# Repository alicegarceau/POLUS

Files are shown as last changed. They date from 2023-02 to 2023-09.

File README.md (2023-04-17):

# POLUS

Démonstrations des habiletés de P-O le petit robot :

<a href="http://www.youtube.com/watch?feature=player_embedded&v=78BupOIvDnI
" target="_blank">Dessin pixels</a>

<a href="http://www.youtube.com/watch?feature=player_embedded&v=hgMGZM_LDB8
" target="_blank">Dessin lignes</a>

## Table des matières
* [Requis matériels](#requis-matériels)
* [Assemblage](#assemblage)
* [Requis logiciels](#requis-logiciels)
* [Installation](#installation)
* [Exécuter le programme](#exécuter-le-programme)
* [License](#license)

## Requis matériels
### Impression 3D
Sur une imprimante 3D avec une capacité d'au moins 250 x 250 x 200mm, imprimer tous les fichiers dans le dossier ([STLs](https://github.com/alicegarceau/POLUS/tree/main/V1_STLs))

### Autres composants mécaniques
- [ ] 1 x Paquet de crayons feutres ([Amazon](https://www.amazon.ca/-/fr/dp/B01LXRJKVY?psc=1&))
- [ ] 2 x Vis M6 x 1 à épaulement de 8 x 55mm ([McMaster-Carr](https://www.mcmaster.com/92981A210/))
- [ ] 2 x Écrous M6
- [ ] 4 x Rondelles M6
- [ ] 1 x Coupleur flexible 5mm à 8mm ([Amazon](https://www.amazon.ca/AFUNTA-Flexible-Couplings-Compatible-Machines/dp/B07JL1QYLS/))
- [ ] 1 x Vis ACME Tr8 x 8mm x 300mm et écrou ([Amazon](https://www.amazon.ca/dp/B08JQ4H6M9?_encoding=UTF8&psc=1&))
- [ ] 3 x Roulements à billes linéaires LM8UU ([Amazon](https://www.amazon.ca/uxcell%C2%AE-Bushing-Linear-Motion-Double/dp/B00X9H22SO/))
- [ ] 4 x Roulements à billes à épaulement 608 ([McMaster-Carr](https://www.mcmaster.com/57155K513/))
- [ ] 26 x Inserts filetés M3 pour plastique ([McMaster-Carr](https://www.mcmaster.com/94180A333/))
- [ ] 32 x Vis SHCS M3 x 14mm
- [ ] 12 x Vis SHCS M2.5 x 6mm
- [ ] 1 x Feuille de contre-plaqué 480 x 480mm
- [ ] 6 x Attaches de plastique (Tyrap) 3 x 100mm min

### Composants électriques
- [ ] 1 x Fil micro-USB de 0.3m
- [ ] 1 x Microcontrôleur OpenCR 1.0 
- [ ] 2 x Servomoteurs Dynamixel XM430-W350
- [ ] 1 x Servomoteur Dynamixel XL430-W250
- [ ] 2 x Servomoteur de type "hobby" Hitech HS-422
- [ ] 1 x Moteur pas-à-pas NEMA17 ([Amazon](https://www.amazon.ca/dp/B06ZYQNBFR?))
- [ ] 1 x Contrôleur de moteur pas-à-pas ([EasyDriver](https://www.sparkfun.com/products/12779))
- [ ] 2 x Interrupteur de fin de course miniature

## Assemblage
### Assemblage électrique
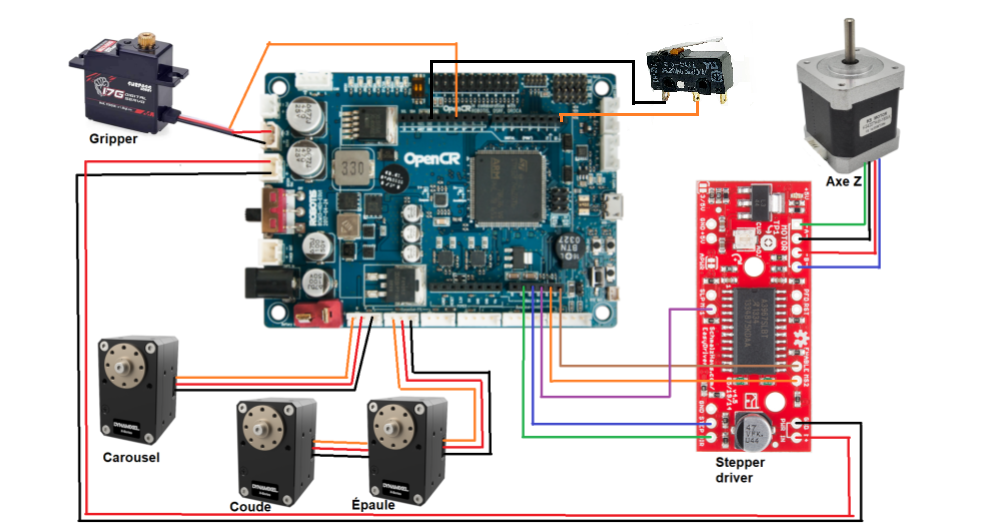
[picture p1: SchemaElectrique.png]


### Assemblage mécanique

Installer les inserts filetés avec un fer à souder à environ 300 deg C dans toutes les pièces qui doivent en recevoir.

#### Avant-bras et pince

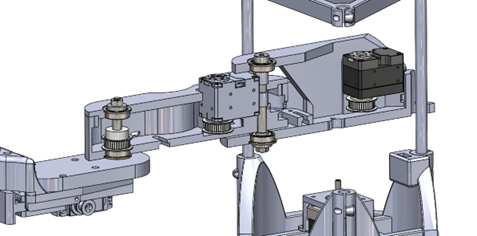
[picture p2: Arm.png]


#### Bras et épaule (plateforme mobile en Z)

#### Base
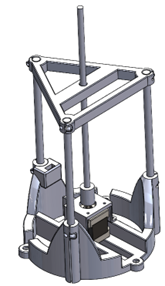
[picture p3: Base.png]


#### Carousel
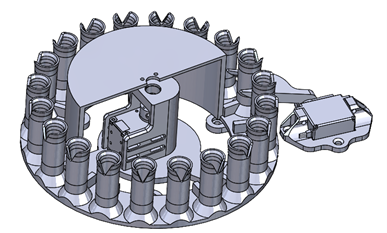
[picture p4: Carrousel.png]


## Requis logiciels
* Arduino IDE version 2 ([arduino](https://www.arduino.cc/en/software))
* Paquet Open-CR du Boards Manager : suivre les instructions d'installation pour Windows ([opencr](https://emanual.robotis.com/docs/en/parts/controller/opencr10/#install-on-windows))

### Fichiers de code du OpenCR
Le dossier Code_OpenCR contient toutes les fonctions en C++ qui s'exécutent sur la carte OpenCR.
- __actuators.cpp__ : Ce fichier contient les fonctions qui contrôlent les actuateurs du projet POLUS, sauf le moteur pas à pas de l'axe Z.
- __stepperZ.cpp__ : Ce fichier contient les fonctions qui contrôlent le moteur pas à pas de l'axe Z. 
- __inverseKinematics.cpp__ : Ce fichier reçoit en entré une valeur cartésienne (X,Y) et retourne deux angles pour les moteurs du bras scara.
- __serialcomm_functions.cpp__: Permet de lire des données depuis un port série, les diviser en parties distinctes et appeler la fonction correspondante en fonction du type de message envoyé.
- __Code_OpenCR.ino__ : Ce fichier est le fichier "main" s'exécutant sur la carte OpenCR.

### Diagramme d'état du code

L'image suivante démontre la relation entre le code s'exécutant sur l'ordinateur (interface utilisateur) et la carte OpenCR.

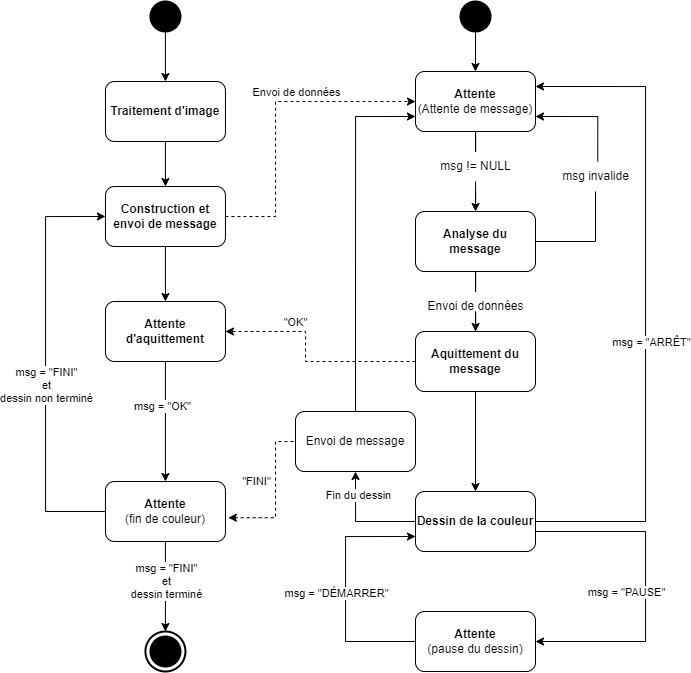
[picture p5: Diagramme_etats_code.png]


## Installation

Sur un PC Windows :
* Ouvrir le fichier Code_OpenCR.ino dans Arduino IDE et brancher la carte OpenCR à l'ordinateur. Dans Arduino IDE, sélectionner le "board" OpenCR et téléverser le code.
* Brancher la carte OpenCR à votre ordinateur avec un fil micro-USB
* Installer les librairies Python suivantes avec pip:
   - pyserial
   - threading
   - PIL
   - os
   - csv
   - numpy
   - colormath
   - tkinter

## Exécuter le programme
- Lancer le programme main.py
- L'interface utilisateur suivant s'ouvre :


- Dans l'interface utilisateur, entrer les bonnes informations dans les différents champs :
   *** Précisions :
   - Le fichier des RGB doit être un fichier .CSV où chaque rangée contient les valeur R,G,B d'un crayon du carrousel. La 1ère ligne du fichier correspond au crayon à      l'index 1 et ainsi de suite. C'est de cette manière que le robot sait quel crayon se trouve à quel endroit dans le carrousel.
   - Le nombre de pixels voulus représente le nombre de pixels pour une dimension. Dans cet exemple, l'image dessinée fera 50x50 pixels.
- Appuyer sur les boutons "Envoyer les noms de fichiers" et "Envoyer la résolution de l'image".
- Fermer l'interface graphique pour lancer le traitement d'image.
- Dans le terminal, un message s'affiche pour choisir le port USB pour établir la liaison série avec le OpenCR (ce message peut prendre plusieurs secondes à             s'afficher).
- L'utilisateur n'a plus rien à faire à partir d'ici.

## License
Apache Version 2.0

Voir [LICENSE](LICENSE)

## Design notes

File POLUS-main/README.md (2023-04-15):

# POLUS
Voir le document "Doc traitement image" pour la documentation des fonctions utilisées pour le traitement d'image (pixeliser_image.py).

- __RGB_20.csv__ : document contenant les 20 RGB des crayons disponibles
- __UI.py__ : création de l'interface utilisateur à l'aide de Tkinter
- __input_UI.py__ : fichier obsolète non utilisé
- __pixeliser_image.html__ : html de la documentation du traitement d'image avec pydoc
- __pixeliser_image.py__ : fonctions utilisées pour le traitement d'image
- __communication.py__ : Fonctions pour initialiser une liaison série, trouver un port disponible, construire et envoyer des messages à l'OpenCR, et lire l'acquittement de ces messages.
- __main.py__ : fonction main
- __image_in.jpg__ : image d'origine
- __image_pix.png__ : image pixélisée
- __image_result.png__ : image du résultat attendu
- __UI2.py__ : 2e version du UI, présentement non fonctionnelle. Cette version est plus épurée.

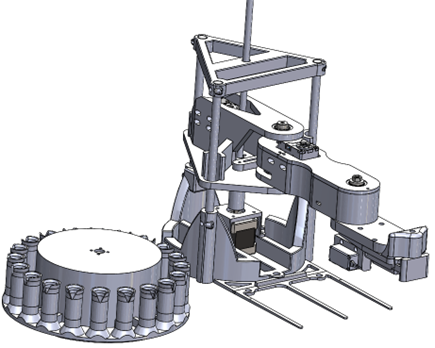
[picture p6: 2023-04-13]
Projet.png

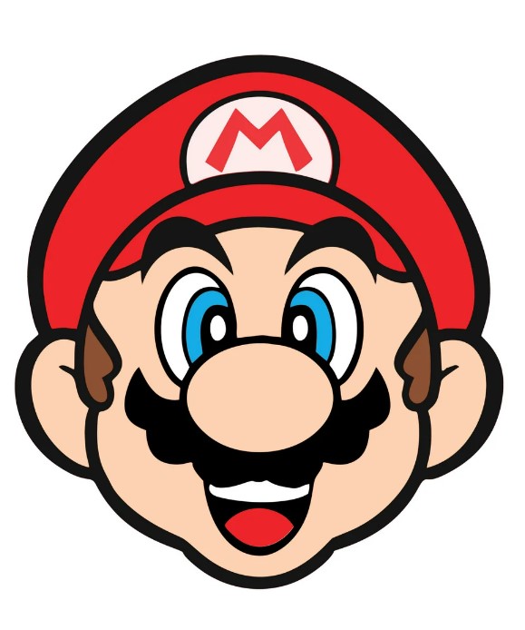
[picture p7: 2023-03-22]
POLUS-main/image_in.jpg

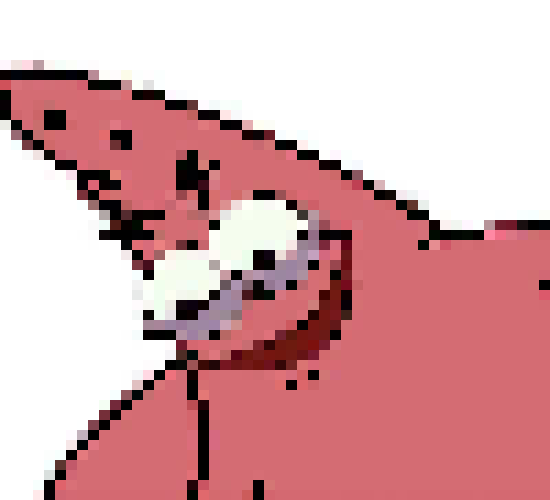
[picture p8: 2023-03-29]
POLUS-main/image_pix.png

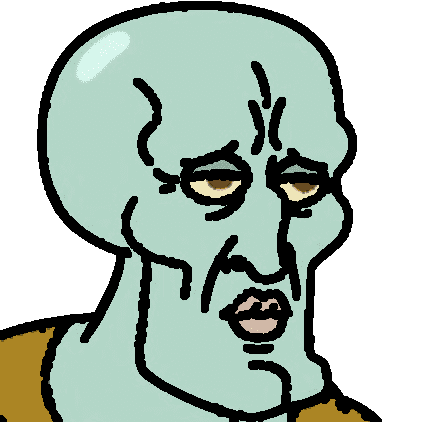
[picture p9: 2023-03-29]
POLUS-main/Carlo1.png

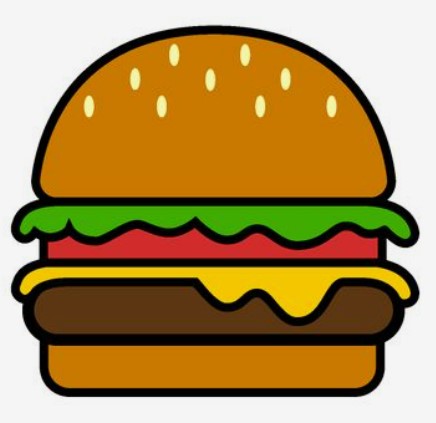
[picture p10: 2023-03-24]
POLUS-main/burger.jpg

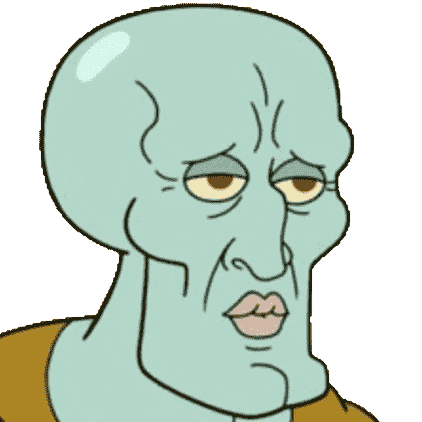
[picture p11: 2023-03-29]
POLUS-main/Carlo.png

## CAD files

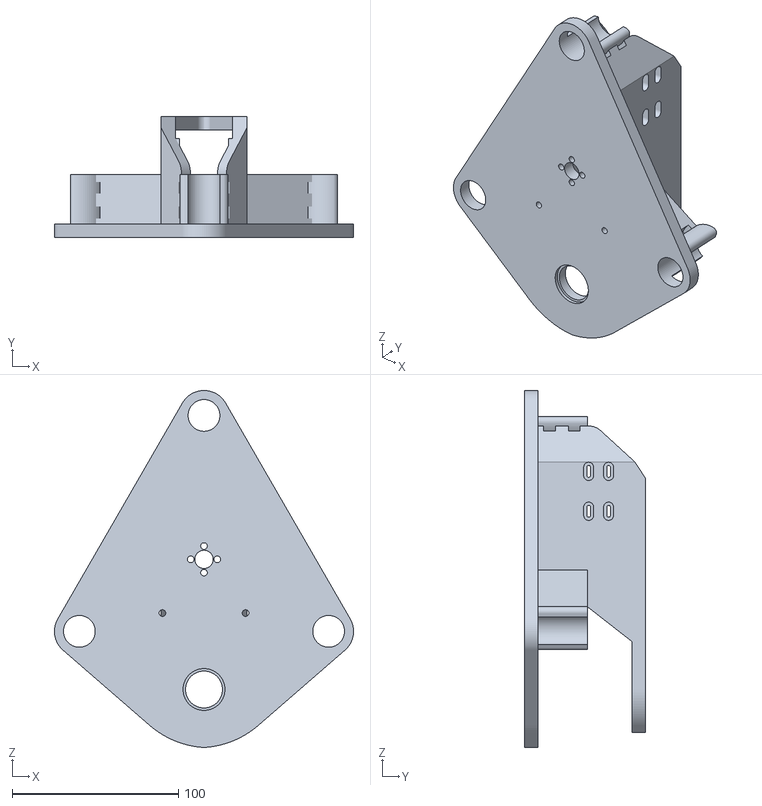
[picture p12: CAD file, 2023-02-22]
V1_STLs/V1_STLs/Arm/PlaqueBottom.STL
180.0 x 72.8 x 214.8

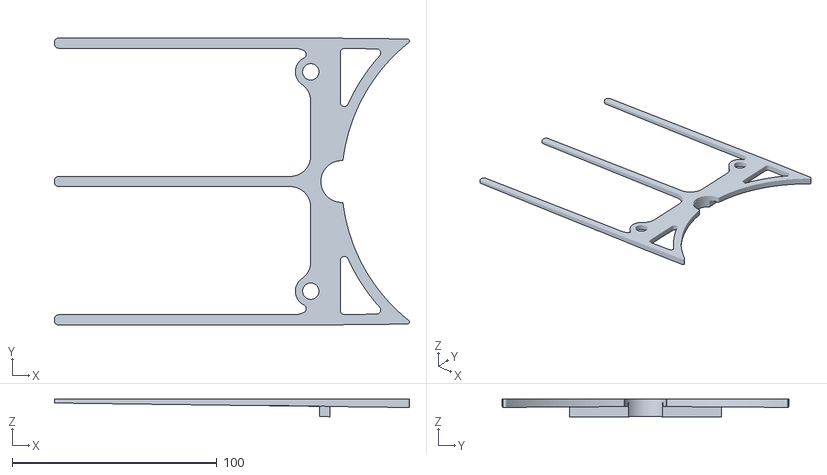
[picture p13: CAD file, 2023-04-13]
V1_STLs/V1_STLs/Base/SpacerV1.STL
173.2 x 140.0 x 8.56

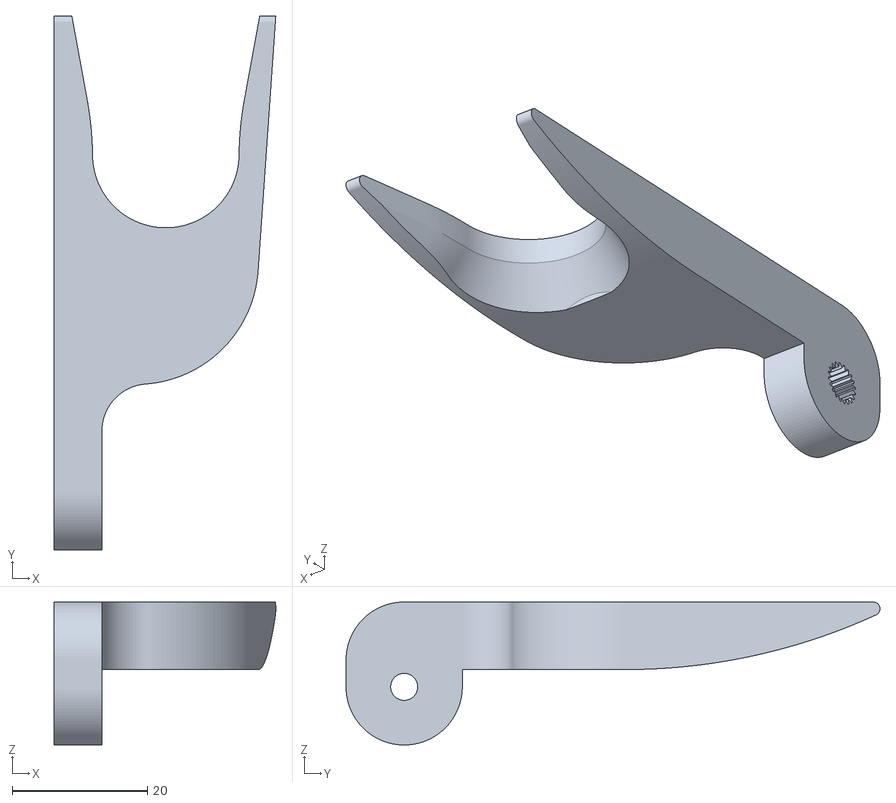
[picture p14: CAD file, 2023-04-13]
V1_STLs/V1_STLs/Carrousel/Centering.STL
32.8 x 79.0 x 21.2

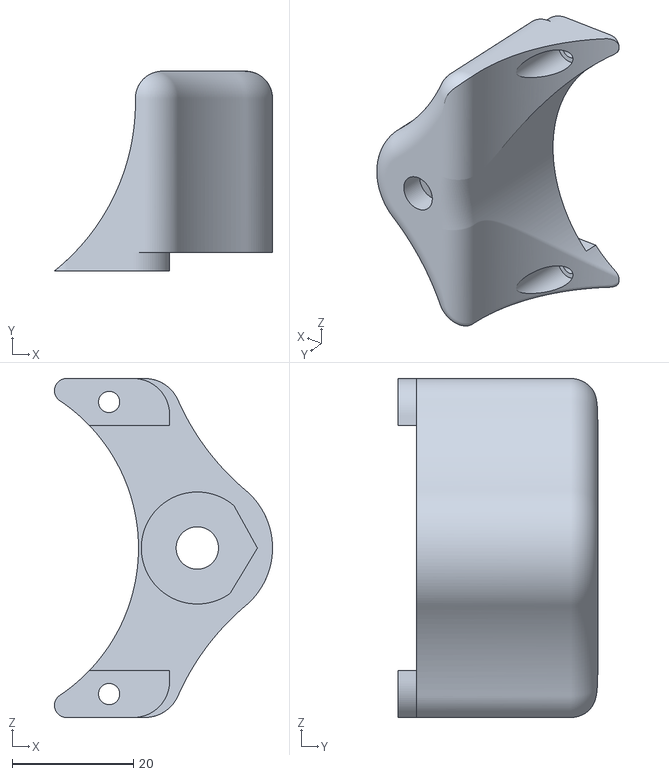
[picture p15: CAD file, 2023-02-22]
V1_STLs/V1_STLs/Pince/SpringCap.STL
36.0 x 33.0 x 56.0

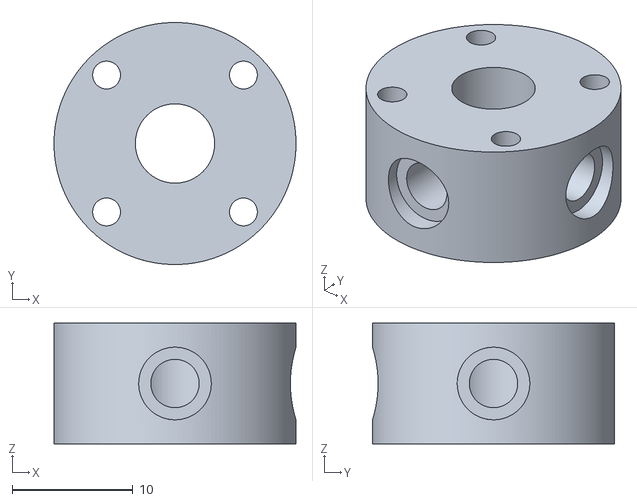
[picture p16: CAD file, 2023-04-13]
V1_STLs/V1_STLs/Pulleys/MotorShaftCoupling.STL
20.0 x 20.0 x 10.0

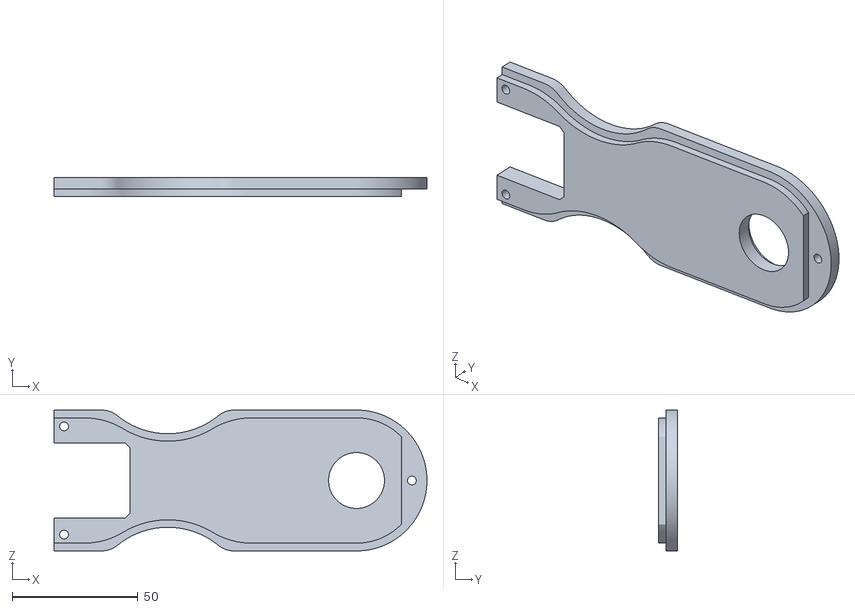
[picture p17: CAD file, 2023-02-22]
V1_STLs/V1_STLs/Arm/Arm1_Cover.STL
148.2 x 7.50 x 56.0

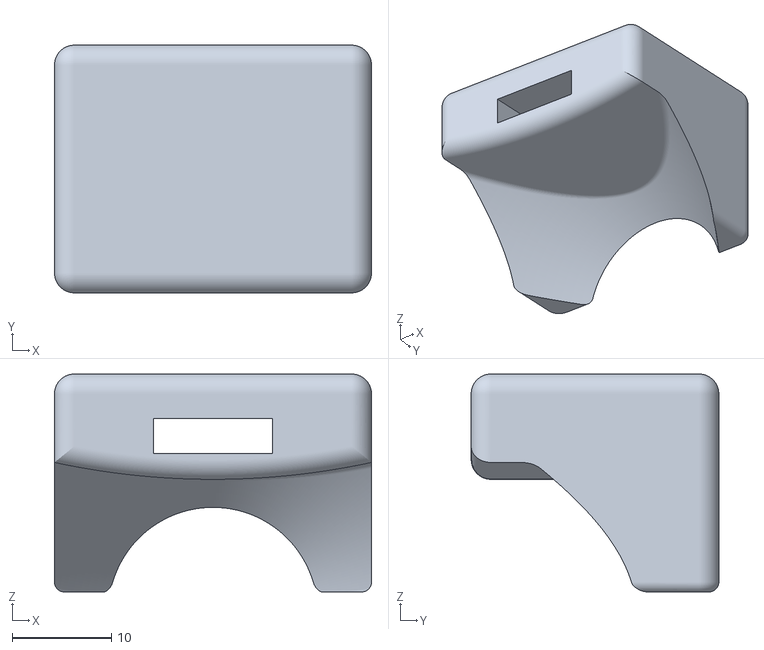
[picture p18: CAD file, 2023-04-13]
V1_STLs/V1_STLs/Base/LimitSwitchMount_V2.STL
32.0 x 25.0 x 22.0

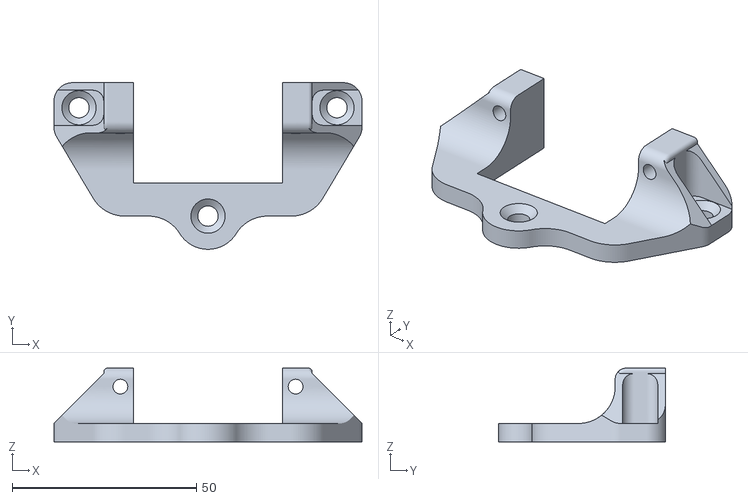
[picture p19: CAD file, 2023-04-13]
V1_STLs/V1_STLs/Carrousel/CenteringServoMount.STL
83.5 x 45.2 x 20.0

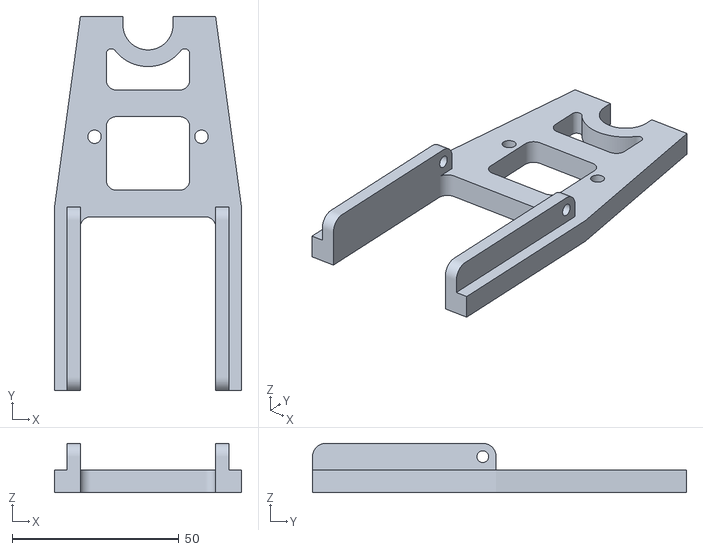
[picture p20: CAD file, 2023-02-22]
V1_STLs/V1_STLs/Pince/ArmMount.STL
56.0 x 112.0 x 14.8

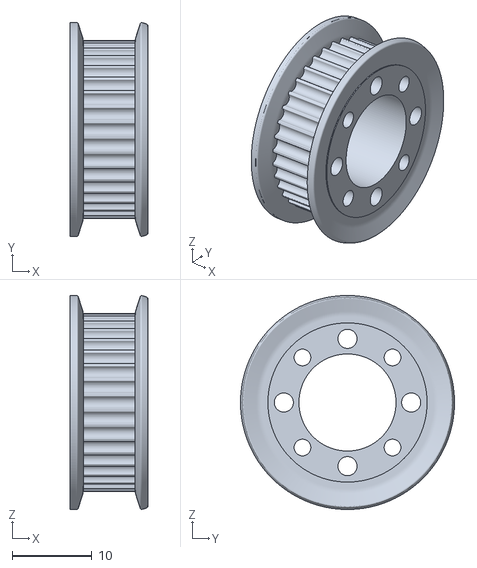
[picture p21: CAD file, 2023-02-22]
V1_STLs/V1_STLs/Pulleys/GT2 36T B5 W10 pulley.stp.STL
9.75 x 26.9 x 26.9

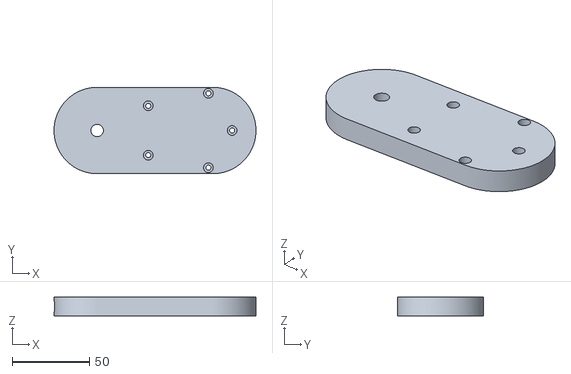
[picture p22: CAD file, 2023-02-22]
V1_STLs/V1_STLs/Arm/Arm2_Shell.STL
131.0 x 56.0 x 12.0

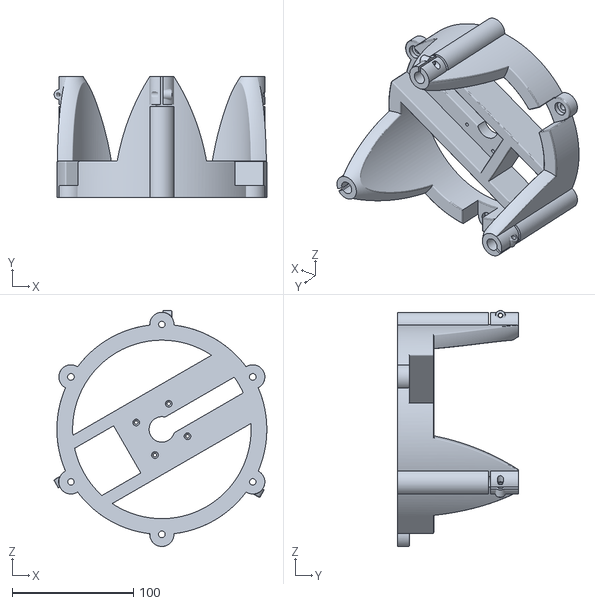
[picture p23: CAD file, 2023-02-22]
V1_STLs/V1_STLs/Base/Base_v4.STL
175.4 x 100.0 x 194.7

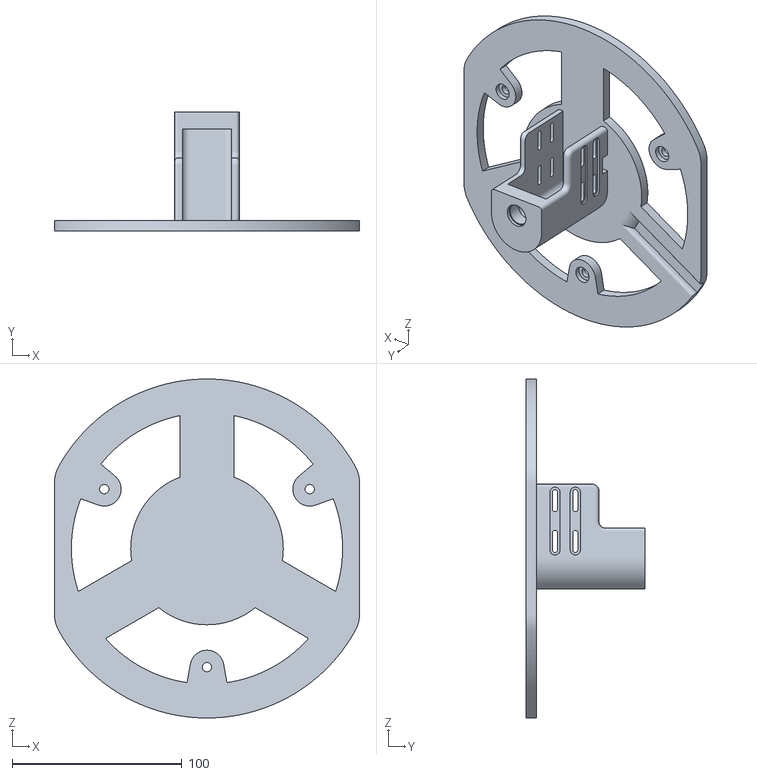
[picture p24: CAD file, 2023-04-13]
V1_STLs/V1_STLs/Carrousel/Carrousel_Base_V3.STL
180.0 x 70.0 x 200.0

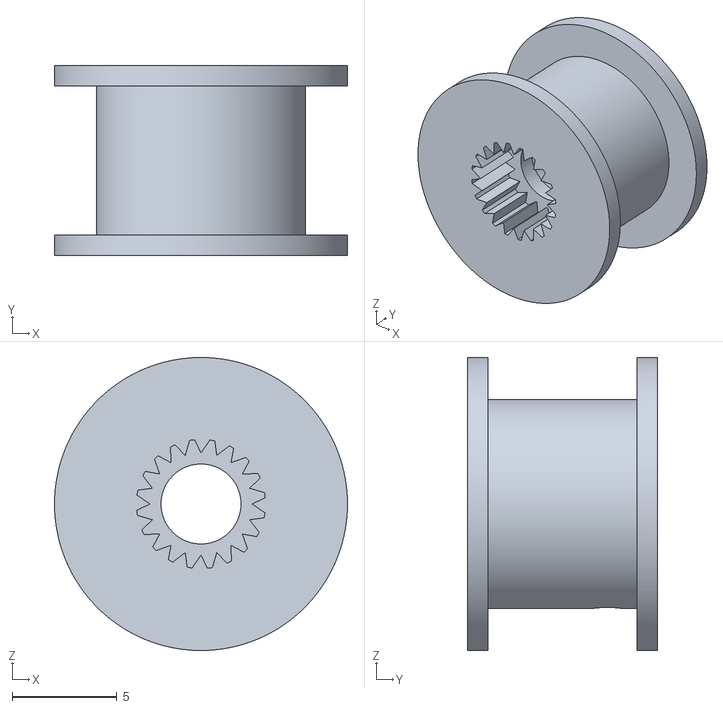
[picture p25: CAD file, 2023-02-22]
V1_STLs/V1_STLs/Pince/Reel.STL
14.0 x 9.10 x 14.0

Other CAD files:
V1_STLs/V1_STLs/Arm/Arm1_Cover2.STL
V1_STLs/V1_STLs/Base/MotorPlate.STL
V1_STLs/V1_STLs/Carrousel/Cloche.STL
V1_STLs/V1_STLs/Pince/JawTest2_2.STL
V1_STLs/V1_STLs/Arm/Arm1_Shell.STL
V1_STLs/V1_STLs/Arm/Tensionner.STL
V1_STLs/V1_STLs/Base/Triangle_Top.STL
V1_STLs/V1_STLs/Pince/Base_V2.STL
V1_STLs/V1_STLs/Pince/JawTest2.STL
V1_STLs/V1_STLs/Pince/Plunger.STL
V1_STLs/V1_STLs/Pince/Spacer.STL
V1_STLs/V1_STLs/Pulleys/GT2 36T Screw.STL
V1_STLs/V1_STLs/Pulleys/GT2-6x60x20.step.STL

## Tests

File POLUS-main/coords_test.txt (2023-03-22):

[2, 50, 50, 921, 922, 923, 924, 925, 971, 972, 973, 974, 975, 976, 977, 1015, 1016, 1017, 1018, 1019, 1022, 1023, 1024, 1025, 1026, 1027, 1029, 1030, 1031, 1032, 1033, 1064, 1065, 1066, 1070, 1071, 1072, 1073, 1074, 1075, 1076, 1077, 1078, 1082, 1083, 1084, 1110, 1111, 1112, 1113, 1114, 1121, 1122, 1123, 1124, 1125, 1126, 1133, 1134, 1135, 1136, 1160, 1161, 1162, 1163, 1164, 1172, 1173, 1174, 1175, 1176, 1184, 1185, 1186, 1187, 1188, 1189, 1209, 1210, 1211, 1212, 1213, 1223, 1224, 1225, 1226, 1235, 1236, 1237, 1238, 1239, 1260, 1261, 1262, 1263, 1264, 1273, 1274, 1275, 1285, 1286, 1287, 1288, 1289, 1310, 1311, 1312, 1313, 1335, 1336, 1337, 1338, 1355, 1356, 1361, 1362, 1363, 1364, 1375, 1385, 1386, 1387, 1392, 1393, 1394, 1404, 1405, 1406, 1412, 1413, 1414, 1420, 1421, 1422, 1423, 1424, 1425, 1426, 1427, 1428, 1435, 1436, 1437, 1442, 1443, 1444, 1445, 1453, 1454, 1455, 1461, 1464, 1465, 1469, 1470, 1471, 1472, 1473, 1474, 1475, 1476, 1477, 1478, 1479, 1480, 1484, 1487, 1493, 1494, 1495, 1503, 1504, 1505, 1506, 1511, 1515, 1518, 1519, 1520, 1521, 1522, 1523, 1524, 1525, 1526, 1527, 1528, 1529, 1530, 1533, 1534, 1537, 1542, 1543, 1544, 1545, 1553, 1554, 1555, 1556, 1561, 1568, 1569, 1570, 1571, 1572, 1573, 1574, 1575, 1576, 1577, 1578, 1579, 1580, 1587, 1592, 1593, 1594, 1595, 1603, 1604, 1605, 1606, 1607, 1610, 1611, 1618, 1619, 1620, 1621, 1622, 1623, 1624, 1625, 1626, 1627, 1628, 1629, 1630, 1638, 1641, 1642, 1643, 1644, 1645, 1654, 1655, 1656, 1657, 1659, 1660, 1661, 1669, 1670, 1671, 1672, 1673, 1674, 1675, 1676, 1677, 1678, 1679, 1687, 1688, 1689, 1691, 1692, 1693, 1694, 1705, 1706, 1707, 1709, 1710, 1711, 1712, 1713, 1720, 1721, 1722, 1723, 1724, 1725, 1726, 1727, 1728, 1736, 1737, 1738, 1741, 1742, 1743, 1744, 1755, 1756, 1757, 1760, 1761, 1762, 1763, 1774, 1785, 1786, 1787, 1788, 1789, 1792, 1793, 1807, 1810, 1811, 1812, 1813, 1814, 1835, 1836, 1837, 1838, 1841, 1860, 1861, 1862, 1863, 1864, 1865, 1866, 1867, 1881, 1882, 1883, 1884, 1885, 1886, 1887, 1888, 1911, 1912, 1913, 1914, 1915, 1916, 1917, 1918, 1930, 1931, 1932, 1933, 1934, 1935, 1936, 1937, 1938, 1962, 1963, 1964, 1965, 1966, 1967, 1968, 1980, 1981, 1982, 1983, 1984, 1985, 1986, 1987, 2013, 2014, 2015, 2016, 2017, 2018, 2030, 2031, 2032, 2033, 2034, 2035, 2065, 2066, 2067, 2068, 2069, 2079, 2080, 2081, 2082, 2083, 2084, 2117, 2118, 2119, 2120, 2129, 2130, 2131, 2169, 2170, 2171, 2178, 2179, 2220, 2221, 2222, 2223, 2225, 2226, 2227, 2228, 2273, 2275, 2276]
[3, 50, 50, 926, 927, 1067, 1115, 1127, 1137, 1138, 1159, 1214, 1222, 1234, 1276, 1314, 1323, 1324, 1325, 1373, 1374, 1376, 1384, 1434, 1456, 1462, 1463, 1485, 1486, 1514, 1516, 1557, 1566, 1581, 1583, 1637, 1662, 1680, 1704, 1729, 1735, 1739, 1759, 1772, 1773, 1775, 1776, 1791, 1834, 1839, 1868, 1880, 1969, 2019, 2029, 2128, 2177, 2180, 2224, 2274]
[4, 50, 50, 220, 229, 281, 282, 334, 421, 422, 423, 424, 425, 426, 427, 428, 469, 470, 471, 474, 475, 478, 479, 518, 519, 520, 528, 530, 557, 568, 569, 572, 573, 575, 576, 579, 580, 606, 618, 619, 622, 624, 627, 631, 668, 669, 671, 672, 673, 674, 675, 676, 677, 679, 680, 681, 692, 952, 996, 1002, 1152, 1320, 1401, 1482, 1651, 1855, 1941, 1974, 2087, 2136, 2183, 2280]
[5, 50, 50, 1796]
[6, 50, 50, 1202, 2165]
[7, 50, 50, 333, 641, 844, 1246, 1332, 2269]
[8, 50, 50, 2038]
[9, 50, 50, 320, 321, 322, 323, 324, 325, 326, 327, 328, 329, 367, 368, 369, 370, 371, 372, 373, 374, 375, 376, 377, 378, 379, 380, 381, 415, 416, 417, 418, 419, 420, 429, 430, 431, 432, 433, 464, 465, 466, 467, 468, 472, 473, 476, 477, 480, 481, 482, 483, 484, 485, 512, 513, 514, 515, 516, 517, 521, 522, 523, 524, 525, 526, 527, 531, 532, 533, 534, 535, 536, 561, 562, 563, 564, 565, 566, 567, 570, 571, 574, 577, 578, 581, 582, 583, 584, 585, 586, 587, 610, 611, 612, 613, 614, 615, 616, 617, 620, 621, 628, 629, 633, 634, 635, 636, 637, 638, 659, 660, 661, 662, 663, 664, 665, 666, 667, 670, 678, 682, 683, 684, 685, 686, 687, 688, 689, 708, 709, 710, 711, 712, 713, 714, 715, 716, 717, 718, 723, 731, 732, 733, 734, 735, 736, 737, 738, 739, 740, 757, 758, 759, 760, 761, 762, 763, 764, 765, 770, 771, 772, 773, 774, 775, 776, 777, 778, 779, 784, 785, 786, 787, 788, 789, 790, 791, 806, 807, 808, 809, 810, 811, 812, 813, 817, 818, 819, 820, 821, 822, 823, 824, 825, 826, 827, 828, 829, 830, 831, 832, 835, 836, 837, 838, 839, 840, 841, 842, 856, 857, 858, 859, 860, 861, 869, 870, 877, 878, 879, 887, 888, 889, 890, 891, 892, 905, 906, 907, 908, 909, 910, 935, 938, 939, 940, 941, 942, 943, 955, 956, 957, 958, 959, 962, 963, 986, 989, 990, 991, 992, 993, 1005, 1006, 1007, 1008, 1009, 1011, 1012, 1036, 1037, 1039, 1040, 1041, 1042, 1043, 1044, 1054, 1055, 1056, 1057, 1058, 1090, 1091, 1092, 1093, 1094, 1104, 1105, 1106, 1107, 1141, 1142, 1143, 1144, 1154, 1155, 1156, 1157, 1191, 1192, 1193, 1194, 1196, 1205, 1206, 1207, 1241, 1242, 1243, 1244, 1253, 1255, 1256, 1271, 1292, 1293, 1294, 1303, 2023, 2024, 2025, 2072, 2073, 2074, 2075, 2076, 2123, 2124, 2125, 2126, 2166, 2175]     
[11, 50, 50, 1119, 1168, 1169, 1170, 1178, 1179, 1180, 1217, 1218, 1219, 1230, 1231, 1267, 1268, 1280, 1281, 1317, 1318, 1330, 1331, 1367, 1368, 1380, 1381, 1417]
[12, 50, 50, 228, 411, 437, 853, 895, 1046, 1117, 1130, 1181, 1283, 1296, 1333, 1346, 1697, 1893, 1908, 1959, 2328]
[13, 50, 50, 1120, 1129, 1431]
[14, 50, 50, 316, 607, 793, 903, 1171, 1220, 1221, 1227, 1228, 1229, 1269, 1279, 1319, 1329, 1369, 1418, 1430, 1920, 1921, 1927, 1928, 1970]
[17, 50, 50, 268, 280, 319, 382, 463, 560, 588, 609, 632, 639, 658, 690, 707, 719, 724, 725, 726, 729, 730, 766, 768, 769, 780, 783, 814, 816, 855, 862, 864, 865, 868, 871, 872, 873, 874, 875, 876, 880, 883, 884, 886, 893, 911, 913, 928, 937, 954, 960, 968, 985, 988, 994, 1004, 1013, 1061, 1062, 1063, 1086, 1087, 1096, 1108, 1109, 1140, 1146, 1158, 1204, 1254, 1257, 1272, 1284, 1291, 1305, 1306, 1308, 1321, 1322, 1326, 1343, 1358, 1359, 1371, 1372, 1377, 1389, 1390, 1407, 1408, 1409, 1410, 1439, 1440, 1458, 1459, 1460, 1488, 1489, 1490, 1508, 1509, 1510, 1512, 1517, 1531, 1532, 1536, 1538, 1539, 1540, 1559, 1560, 1565, 1567, 1582, 1589, 1590, 1596, 1639, 1668, 1686, 1719, 1758, 1764, 1777, 1815, 1833, 1892, 1919, 2070, 2077, 2121, 2122, 2127, 2172, 2173, 2174, 2176, 2279]
[18, 50, 50, 221, 222, 223, 224, 225, 226, 227, 267, 315, 363, 385, 412, 436, 460, 488, 509, 539, 558, 590, 656, 705, 743, 754, 945, 966, 967, 978, 980, 981, 982, 1020, 1021, 1028, 1034, 1052, 1068, 1069, 1079, 1080, 1081, 1085, 1102, 1116, 1128, 1132, 1139, 1165, 1166, 1177, 1183, 1215, 1233, 1259, 1265, 1270, 1278, 1315, 1328, 1334, 1352, 1354, 1365, 1378, 1383, 1388, 1396, 1403, 1411, 1415, 1429, 1433, 1447, 1451, 1466, 1467, 1468, 1481, 1483, 1492, 1496, 1501, 1507, 1546, 1551, 1588, 1591, 1597, 1601, 1608, 1609, 1631, 1647, 1653, 1658, 1695, 1702, 1746, 1753, 1771, 1794, 1795, 1804, 1805, 1806, 1808, 1809, 1840, 1842, 1843, 1844, 1856, 1857, 1889, 1891, 1909, 1910, 1922, 1923, 1924, 1925, 1926, 1929, 1940, 1961, 1971, 1972, 1973, 1975, 1976, 1977, 1978, 1979, 1989, 2010, 2012, 2036, 2061, 2062, 2064, 2085, 2113, 2114, 2115, 2116, 2132, 2133, 2134, 2135, 2167, 2168, 2181, 2182, 2217, 2218, 2219, 2229, 2230, 2231, 2270, 2271, 2272, 2277, 2278, 2320, 2321, 2322, 2323, 2324, 2325, 2326, 2327]

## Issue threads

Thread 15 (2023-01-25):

Modéliser la cinématique inverse

FredDesaulniers, 2023-01-25:
- [ ] Image du squelette du robot avec dimensions et identification des éléments (membre = ligne, joint = point)
- [ ] Matrice inverse
- [ ] Mettre sous forme de code dans MatInverse.hpp (s'inspirer de [Scarus](https://github.com/UdeS-GRO/S4H2021-Scarus))

Closed 2023-02-22.

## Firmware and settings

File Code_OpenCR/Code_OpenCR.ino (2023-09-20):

/*
Projet: POLUS
Description: Méthode principale (main) qui gère la communication et les actions du robot à haut niveau
Auteurs: Frédérik Desaulniers – DESF3105
         Pierre-Olivier Dupont – DUPP2408
         Alice Garceau – GARA2507
         Enrick Hébert – HEBE2701
         Émile Michaud – MICE1602

Inspiré du travail original de :
Projet:     SCARUS
Auteurs: Alec Gagnon,      gaga2120
         Étienne Lefebvre, lefe1001
         Robin Mailhot,    mair1803
         Charles Caya,     cayc2401
*/

// ---------- Libraries ----------
#include "actuators.hpp"
#include "inverseKinematics.hpp"
#include "serialcomm_functions.hpp"
#include <pthread.h>
#include "UDES2.h"
#include "robo.h"
#include "dessin1.h"
#include "dessin2.h"
#include "dessin3.h"


/*#include "comm_functions.hpp"
#include "inverse_kinematics.hpp"
*/


// ---------- Enumerations ----------
enum class State { Sleep, Wait, Parse, Moving };

// ---------- Constants ----------
// --- Motors ---
//epaule ID = 20, coude ID = 15, caroussel ID = 3 from: Example/Dynamixel2Arduino/Basic/ScanDynamixel
const std::vector<uint8_t> MOTOR_IDS_ARM = { (const uint8_t)20, (const uint8_t)15 }; 
const std::vector<uint8_t> MOTOR_IDS_CAR = { (const uint8_t)2 };

const uint8_t nbAvailableColors = 20;
const uint8_t nbColumn = 50;

const uint8_t SERVO_PIN = 11;
const uint8_t SERVO_CAR = 9;

const float lineDraw = 21.7;
const float lineApproach = 24;

// ---------- Variables ----------
// --- Motors ---
DynamixelWorkbench dynaArm;
DynamixelWorkbench dynaCar;
Servo servoGripper; 
Servo servoCarrousel; 

float ZOffset = 0;
int dessin = 0;


// --- Data ---
State current_state = State::Sleep;
String msg = String();
float motor_angles_arm[2] = {0, 0};
int stepCurrentPos = 0;

int colorIndex = 0;

// ---------- Main functions ----------
void setup()
{
  //comm_init();
  
  const int BAUDRATE = 115200;
  Serial.begin(BAUDRATE);
  setupStepper();

  init_motors(dynaArm, MOTOR_IDS_ARM);
  init_motors(dynaCar, MOTOR_IDS_CAR);

  pinMode(SERVO_PIN, OUTPUT);
  pinMode(SERVO_CAR, OUTPUT);

  

  servoGripper.attach(SERVO_PIN);
  servoCarrousel.attach(SERVO_CAR);
  inverse_kinematics(0, 150, motor_angles_arm);
  move_to_pos_wait(dynaArm, MOTOR_IDS_ARM, motor_angles_arm);
  index_color(dynaCar, MOTOR_IDS_CAR, servoCarrousel,  1);

  if (digitalRead(BDPIN_PUSH_SW_1) == FALSE && digitalRead(BDPIN_PUSH_SW_2) == FALSE) 
  {
    dessin = 1;
  } else if (digitalRead(BDPIN_PUSH_SW_1) == TRUE && digitalRead(BDPIN_PUSH_SW_2) == FALSE)
  {
    dessin = 2;
  } else if (digitalRead(BDPIN_PUSH_SW_1) == FALSE && digitalRead(BDPIN_PUSH_SW_2) == TRUE)
  {
    dessin = 3;
  } else if (digitalRead(BDPIN_PUSH_SW_1) == TRUE && digitalRead(BDPIN_PUSH_SW_2) == TRUE)
  {
    dessin = 4;
  }
  homeZ();
  Serial.println("------------------- NEW PROGRAM ----------------");

}

void loop()
{


  
  int column = 50;
  int nbpts = 0;
  if (dessin == 1)
  {
    int dessin1Size =  sizeof(dessin1)/4;
    for (int i = 0; i < dessin1Size ; i++)
    {
      int color = dessin1[i + 1];
      int j = 2;
      while(TRUE)
      {
        if (dessin1[i+j] == 10000 || dessin1[i+j] == 12000)
        {
          nbpts = j-2;
          break;
        } 
        j++;
      }
      int Coord[nbpts];
      for (int t=0; t < nbpts+1; t++)
      {
        Coord[t] = dessin1[i+t+2];
      } 
      pixelisation(Coord, nbpts, column, dynaArm, MOTOR_IDS_ARM, motor_angles_arm, 
      servoGripper, dynaCar, MOTOR_IDS_CAR, servoCarrousel, color); 
      i = i+nbpts+1;
      if (dessin1[i+1] == 12000)
      {
        break;
      }
      delay(1000);
    }
  }

  if (dessin == 2)
  {
    int dessin2Size =  sizeof(dessin2)/4;
    for (int i = 0; i < dessin2Size ; i++)
    {
      int color = dessin2[i + 1];
      int j = 2;
      while(TRUE)
      {
        if (dessin2[i+j] == 10000 || dessin2[i+j] == 12000)
        {
          nbpts = j-2;
          break;
        } 
        j++;
      }
      int Coord[nbpts];
      for (int t=0; t < nbpts+1; t++)
      {
        Coord[t] = dessin2[i+t+2];
      } 
      pixelisation(Coord, nbpts, column, dynaArm, MOTOR_IDS_ARM, motor_angles_arm, 
      servoGripper, dynaCar, MOTOR_IDS_CAR, servoCarrousel, color); 
      i = i+nbpts+1;
      if (dessin2[i+1] == 12000)
      {
        break;
      }
      delay(1000);
    }
  }

  if (dessin == 3)
  {
    int dessin3Size =  sizeof(dessin3)/4;
    for (int i = 0; i < dessin3Size ; i++)
    {
      int color = dessin3[i + 1];
      int j = 2;
      while(TRUE)
      {
        if (dessin3[i+j] == 10000 || dessin3[i+j] == 12000)
        {
          nbpts = j-2;
          break;
        } 
        j++;
      }
      int Coord[nbpts];
      for (int t=0; t < nbpts+1; t++)
      {
        Coord[t] = dessin3[i+t+2];
      } 
      pixelisation(Coord, nbpts, column, dynaArm, MOTOR_IDS_ARM, motor_angles_arm, 
      servoGripper, dynaCar, MOTOR_IDS_CAR, servoCarrousel, color); 
      i = i+nbpts+1;
      if (dessin3[i+1] == 12000)
      {
        break;
      }
      delay(1000);
    }
  }
    
  if (dessin == 4)
  {
    index_color(dynaCar, MOTOR_IDS_CAR, servoCarrousel,  15);
    pick(servoGripper, dynaArm, MOTOR_IDS_ARM, motor_angles_arm);

    inverse_kinematics( UDES2[0][0] , UDES2[0][1], motor_angles_arm);
    move_to_pos_wait(dynaArm, MOTOR_IDS_ARM, motor_angles_arm);
    stepperGoToPos(lineDraw);

    for (int i = 0 ; i < (sizeof(UDES2)/sizeof(UDES2[1]))-1 ; i++)
      {
        
        
        inverse_kinematics( UDES2[i][0] , UDES2[i][1], motor_angles_arm);
        move_to_pos_wait(dynaArm, MOTOR_IDS_ARM, motor_angles_arm);

        if ((abs(UDES2[i][0]-UDES2[i+1][0]) > 2) || (abs(UDES2[i][1]-UDES2[i+1][1]) > 2))
        { 
          Serial.println("MOVE");
          stepperGoToPos(lineApproach);
          delay(200);
          inverse_kinematics( UDES2[i+1][0] , UDES2[i+1][1], motor_angles_arm);
          move_to_pos_wait(dynaArm, MOTOR_IDS_ARM, motor_angles_arm);
          stepperGoToPos(lineDraw);
          delay(200);
        }
      
      }

      place(servoGripper, dynaArm, MOTOR_IDS_ARM, motor_angles_arm);
      index_color(dynaCar, MOTOR_IDS_CAR, servoCarrousel,  19);
      pick(servoGripper, dynaArm, MOTOR_IDS_ARM, motor_angles_arm);
      inverse_kinematics( robo[0][0] , robo[0][1], motor_angles_arm);
      move_to_pos_wait(dynaArm, MOTOR_IDS_ARM, motor_angles_arm); 
      stepperGoToPos(lineDraw);

    for (int i = 0 ; i < (sizeof(robo)/sizeof(robo[1]))-1 ; i++)
      {
        
        
        inverse_kinematics( robo[i][0] , robo[i][1], motor_angles_arm);
        move_to_pos_wait(dynaArm, MOTOR_IDS_ARM, motor_angles_arm);

        if ((abs(robo[i][0]-robo[i+1][0]) > 2) || (abs(robo[i][1]-robo[i+1][1]) > 2))
        { 
          Serial.println("MOVE");
          stepperGoToPos(lineApproach);
          delay(200);
          inverse_kinematics( robo[i+1][0] , robo[i+1][1], motor_angles_arm);
          move_to_pos_wait(dynaArm, MOTOR_IDS_ARM, motor_angles_arm);
          stepperGoToPos(lineDraw);
          delay(200);
        }
      
      }
    place(servoGripper, dynaArm, MOTOR_IDS_ARM, motor_angles_arm);
  }
delay(10000000);

}

  ///////////////////////////////// CALIBRATION POSITIONS /////////////////////////////////
    /*
  inverse_kinematics(-157.31, 92.50, motor_angles_arm);
  move_to_pos_wait(dynaArm, MOTOR_IDS_ARM, motor_angles_arm);
  index_color(dynaCar, MOTOR_IDS_CAR, servoCarrousel, 2);
  while(1){
    getArmMotorAngles(dynaArm, MOTOR_IDS_ARM, motor_angles_arm);
    delay(1000);  
  }
  */
/////////////////////////////////////////////////////////////////////////////////////////


/////////////////////////////// Dessin with troubleshooting prints /////////////////////
/*
  if (dessin == 1)
  {
    int dessin1Size =  sizeof(dessin1)/4;
    Serial.println(dessin1Size);
    for (int i = 0; i < dessin1Size ; i++)
    {
      
      int color = dessin1[i + 1];
      int j = 2;
      Serial.print("Color : ");
      Serial.println(color);
      while(TRUE)
      {
        if (dessin1[i+j] == 10000 || dessin1[i+j] == 12000)
        {
          nbpts = j-2;
          break;
        } 
        j++;
      }
      Serial.println(nbpts);
      int Coord[nbpts];

      for (int t=0; t < nbpts+1; t++)
      {
        Coord[t] = dessin1[i+t+2];
      } 
      for (int r = 0; r < nbpts; r++)
      {
        Serial.print(r);
        Serial.print(" : ");
        Serial.println(Coord[r]);
      }
      Serial.print("--crayon done-- i = ");
      i = i+nbpts+1;
      Serial.println(i);
      Serial.print("j = ");
      Serial.println(j);
      Serial.print("final element : ");
      Serial.println(dessin1[i+1]);
      if (dessin1[i+1] == 12000)
      {
        break;
      }
      //pixelisation(Coord, nbpts, column, dynaArm, MOTOR_IDS_ARM, motor_angles_arm, 
      //servoGripper, dynaCar, MOTOR_IDS_CAR, servoCarrousel, color); 
      delay(1000);
    }
  }
*/
  ////////////////////////////////////////////////////////////////////////////////

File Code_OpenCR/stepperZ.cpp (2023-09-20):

/*
Projet: POLUS
Description: Méthode principale (main) qui gère la communication et les actions du robot à haut niveau
Auteurs: Frédérik Desaulniers – DESF3105
         Pierre-Olivier Dupont – DUPP2408
         Alice Garceau – GARA2507
         Enrick Hébert – HEBE2701
         Émile Michaud – MICE1602
*/

#include "stepperZ.hpp"

//Declare variables for functions
const int MAX_MM = 100; // Limit logicielle, hauteur maximale permise par rapport à la position d'origine (interrupteur de fin de course)
const int MIN_MM =   5; // Limit logicielle, hauteur minimale permise par rapport à la position d'origine (interrupteur de fin de course)
static float currPosmm; // Position actuelle en mm
const float OffsetCoeff = 0.0025;

int oneTime = 1;


// Pour deboguage
//Main loop 
//void loop() {
//  while( oneTime ) {
//    homeZ();
//    stepperGoToPos( 20 );
//    delay(5000);
//    stepperGoToPos( 50 );
//    oneTime = 0;
//  }
//}

void setupStepper()
  // À mettre dans la fonction setup du fichier principal
{
  pinMode(PIN_STP, OUTPUT);
  pinMode(PIN_DIR, OUTPUT);
  pinMode(PIN_MS1, OUTPUT);
  pinMode(PIN_MS2, OUTPUT);
  pinMode(PIN_EN, OUTPUT);
  pinMode(PIN_SW, INPUT_PULLUP);
  digitalWrite(PIN_STP, LOW);
  digitalWrite(PIN_DIR, LOW);
  digitalWrite(PIN_MS1, LOW);
  digitalWrite(PIN_MS2, LOW);
  digitalWrite(PIN_EN, HIGH);
}

void resetEDPins()
// Remettre les broches du Easy Driver à leur état de départ (au setup)
{
  digitalWrite(PIN_STP, LOW);
  digitalWrite(PIN_DIR, LOW);
  digitalWrite(PIN_MS1, LOW);
  digitalWrite(PIN_MS2, LOW);
  digitalWrite(PIN_EN, HIGH);
}

void homeZ()
// Retourner à la position d'origine en Z. Descend jusqu'à toucher l'interrupteur de fin de course, puis remonte de MIN_MM.
{
  digitalWrite(PIN_MS1, HIGH);
  digitalWrite(PIN_MS2, HIGH);
  digitalWrite(PIN_EN, LOW);
  digitalWrite(PIN_DIR, LOW);
  while( digitalRead(PIN_SW) != false )
  {
    digitalWrite(PIN_STP,HIGH); // Déclencher un pas
    delayMicroseconds(500);     // Attendre pour le mouvement mécanique du rotor. Delais plus long vs mouvement pour avancer lentement
    digitalWrite(PIN_STP,LOW); // Remettre la broche à l'état BAS, pour pouvoir la réactiver
    delayMicroseconds(500);
  }
  currPosmm = 0;
  //Serial.println(currPosmm);
}

float updateZOffset(float yPos)
{
  float ZOffset;
  ZOffset = yPos * OffsetCoeff;
  return ZOffset;
}

// 1/8th microstep foward mode function
void stepperGoToPos(float goalmm) // goalmm, 
{
// Aller à une position donnée en mm par rapport à la position d'origine. Utilise le mode micro-stepping à 1/8 de pas.


  float displacementmm = goalmm - currPosmm; 
  currPosmm += displacementmm;
  float nMicroStepsFloat = abs((displacementmm / MM_PER_TURN) * STEPS_PER_TURN * MICRO_STEPS);
  int nMicroSteps = round(nMicroStepsFloat);
  int direction;
  if (displacementmm < 0) {
    direction = LOW;
  } else {
    direction = HIGH;
  }
  digitalWrite(PIN_DIR, direction); // Établi l'état BAS ou HAUT de la broche de contrôle de la direction. Dépend du signe de la cible (distmm)
  digitalWrite(PIN_MS1, HIGH); // Établi l'état des broches PIN_MS1 et PIN_MS2 à HAUT pour que le mode micro-stepping soit à 1/8 de pas.
  digitalWrite(PIN_MS2, HIGH);
  digitalWrite(PIN_EN, LOW); // Établi l'état BAS de la broche de désactivation pour permettre le mouvement.

  for(int x= 1; x<nMicroSteps; x++)  
  {
    digitalWrite(PIN_STP,HIGH); // Déclencher un pas
    delayMicroseconds(100);     // Délais minimal de 100 microsecondes pour laisser le temps au rotor d'arriver à sa position de micro-pas
    digitalWrite(PIN_STP,LOW); // Remettre la broche à l'état BAS, pour pouvoir la réactiver
    delayMicroseconds(100);

  }

}

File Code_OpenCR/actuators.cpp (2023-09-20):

/*
Projet: POLUS
Description: Fonctions qui gerent les actuateurs à haut niveau
Auteurs: Frédérik Desaulniers – DESF3105
         Pierre-Olivier Dupont – DUPP2408
         Alice Garceau – GARA2507
         Enrick Hébert – HEBE2701
         Émile Michaud – MICE1602
Fonctions degrees_to_int(), init_motors(), go_to_home_arm(), start_motors(), 
stop_motors(), move_to_pos() et move_to_pos_wait() inspirées du travail original de :
Projet:     SCARUS
Auteurs: Alec Gagnon,      gaga2120
         Étienne Lefebvre, lefe1001
         Robin Mailhot,    mair1803
         Charles Caya,     cayc2401
*/

#include "actuators.hpp"
#include "stepperZ.hpp"
#include "inverseKinematics.hpp"

const int crayonPick = 24;
const int crayonRetreat = 80;
const int crayonApproach = 80;  //60
const int nbAvailableColors = 20;

const int pixelApproach = 23;
const int pixelDraw = 19;

const float epauleRatio = 1.667;
const float degPulse = 0.088;
/*
const float XCarIn = -159.01; 
const float YCarIn = 96.75; 
const float XCarOut = -144.93;
const float YCarOut = 107.01;
*/
const float XCarIn = -157.31; 
const float YCarIn = 92.50; 
const float XCarOut = -134.99;
const float YCarOut = 105.08;


/// Custom function to convert an angle to a value that can be sent
/// to the Dynamixel motors.
int32_t degrees_to_int(const float angle)
{
    return (int32_t)(4095*(angle+180)/360);
}

/// Moves the motors to a wanted position.
void move_to_pos(DynamixelWorkbench& motor, const std::vector<uint8_t>& motor_IDs, float angles[2])
{
    for (size_t i = 0; i < motor_IDs.size(); ++i)
    {
        motor.goalPosition(motor_IDs[i], degrees_to_int(angles[i]));
    }
}

/// Calls move_to_pos and waits until the movements are complete.
bool move_to_pos_wait(DynamixelWorkbench& motor, const std::vector<uint8_t>& motor_IDs, float angles[2])
{
    bool move_complete = false;
    move_to_pos(motor, motor_IDs, angles);
  
    for (int i = 0; i < 100 && !move_complete; ++i)
    {
        int32_t pos0 = 0;
        int32_t pos1 = 0;

        motor.getPresentPositionData(motor_IDs[0], &pos0);
        motor.getPresentPositionData(motor_IDs[1], &pos1);
      
        move_complete = abs(degrees_to_int(angles[0]) - pos0) < 3 && abs(degrees_to_int(angles[1]) - pos1) < 3;
        if (move_complete)
        {
          Serial.println(i);
        }

        
        //Debug
        /*Serial.print(" Epaule asked vs real : ");
        Serial.print(degrees_to_int(angles[0]));
        Serial.print(" ");
        Serial.print(pos0);
        Serial.print(" Coude asked vs real : ");
        Serial.print(degrees_to_int(angles[1]));
        Serial.print(" ");
        Serial.println(pos1);*/
        
        delay(10);
    }
}

void init_motors(DynamixelWorkbench& motor, const std::vector<uint8_t>& motor_IDs)
{
    for (size_t i = 0; i < motor_IDs.size(); ++i)
    {
        const char* motor_name = i+"";
        uint16_t model_number = 0;
        const char* error_message;
        motor.init(motor_name, 57600, &error_message);
        motor.ping(motor_IDs[i], &model_number, &error_message);
        motor.jointMode(motor_IDs[i], 150, 0, &error_message);
        motor.torqueOn(motor_IDs[i]);
    }
}

void go_to_home_arm(DynamixelWorkbench& motor, const std::vector<uint8_t>& motor_IDs, float motor_angles[2])
{
    for (int i = 0; i < motor_IDs.size(); ++i)
    {
        motor_angles[i] = 0;
    }
    delay(1000);
    move_to_pos_wait(motor, motor_IDs, motor_angles);
}

void start_motors(DynamixelWorkbench& motor, const std::vector<uint8_t>& motor_IDs)
{
    for (size_t i = 0; i < motor_IDs.size(); ++i)
    {
        motor.torqueOn(motor_IDs[i]);
    }
}

void stop_motors(DynamixelWorkbench& motor, const std::vector<uint8_t>& motor_IDs)
{
    for (size_t i = 0; i < motor_IDs.size(); ++i)
    {
        motor.torqueOff(motor_IDs[i]);
    }
}

void open_gripper(Servo& servoGripper)
{
  while(servoGripper.read()!=145)
  {
    servoGripper.write(145);
  }
}

void close_gripper(Servo& servoGripper)
{
  while(servoGripper.read()!=0)
  {
    servoGripper.write(0);
  }
    
}


void index_color(DynamixelWorkbench& motor, const std::vector<uint8_t>& motor_IDs, Servo& servoCarrousel, int colorIndex)
{
    if(colorIndex >= nbAvailableColors)
    {
        Serial.println("Erreur: Index hors de la plage permise");
    }
    else{
      while(servoCarrousel.read()!=70)
      {
        servoCarrousel.write(70);
      }
    delay(500);
    float angleDivision = 360.0 / static_cast<float>(nbAvailableColors); 
    float carAngle = (static_cast<float>(colorIndex)*(angleDivision))-180;
    move_to_pos_wait(motor, motor_IDs, &carAngle);
    while(servoCarrousel.read()!=150)
      {
        servoCarrousel.write(150);
      }
      delay(500);
    }

}

void pick(Servo& servoGripper, DynamixelWorkbench& motor, const std::vector<uint8_t> motor_IDs, float angles[2])
{
  stepperGoToPos(crayonApproach);
  inverse_kinematics( XCarIn , YCarIn, angles);
  move_to_pos_wait(motor, motor_IDs, angles);
  open_gripper(servoGripper);
  stepperGoToPos(crayonPick);
  close_gripper(servoGripper);
  delay(2000);
  stepperGoToPos(crayonRetreat);

  for (float i = 0; i<=1; i += 0.05)
  {
    float moveX = abs((XCarIn - XCarOut)*i);
    float moveY = abs((YCarIn - YCarOut)*i);
    inverse_kinematics( XCarIn + moveX, YCarIn + moveY, angles);
    move_to_pos_wait(motor, motor_IDs, angles);
  }

}

void place(Servo& servoGripper, DynamixelWorkbench& motor, const std::vector<uint8_t> motor_IDs, float angles[2])
{
  stepperGoToPos(crayonRetreat);

  for (float i = 0; i<=1; i += 0.05)
  {
    float moveX = abs((XCarIn - XCarOut)*i);
    float moveY = abs((YCarIn - YCarOut)*i);
    inverse_kinematics( XCarOut - moveX, YCarOut -  moveY, angles);
    move_to_pos_wait(motor, motor_IDs, angles);
  }

  open_gripper(servoGripper);
  delay(1000);
}

void pixel_to_pos(int pixel, float pixelPos[2], int nbColumn)
{
  int goalRow = pixel / nbColumn;
  int goalColumn = pixel - (goalRow*nbColumn);
  pixelPos[0] = -75 + (goalColumn * 3);
  pixelPos[1] = 250 - (goalRow * 3);
}

void drawPoint(DynamixelWorkbench& motor, const std::vector<uint8_t> motor_IDs, float angles[2], int pixel, int nbColumn)
{
  
  float pixelPos[2];
  pixel_to_pos(pixel, pixelPos, nbColumn);
  inverse_kinematics( pixelPos[0] , pixelPos[1], angles);
  move_to_pos_wait(motor, motor_IDs, angles);
  stepperGoToPos(pixelDraw);
  delay(50);
  stepperGoToPos(pixelApproach);
}
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

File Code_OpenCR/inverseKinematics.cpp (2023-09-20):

/*
Projet: POLUS
Description: Fonctions qui gerent la cinematique inverse du robot 
Auteurs: Frédérik Desaulniers – DESF3105
         Pierre-Olivier Dupont – DUPP2408
         Alice Garceau – GARA2507
         Enrick Hébert – HEBE2701
         Émile Michaud – MICE1602
*/

#include "inverseKinematics.hpp"
const float epauleRatio = 1.667;
const float LA = 150; //mm
const float LB = 114.78; //mm
const float epauleZeroOffset = -3.05; //-2.73
const float coudeZeroOffset = 2.33; //1.97

void inverse_kinematics(float x, float y, float THETA[2])
{
    // S'assurer que les coordonnées en entrée sont atteignables
    if ((y >= 0) && ( sqrt(pow(x,2) + pow(y,2)) <= 264.78 ) && (sqrt(pow(x,2) + pow(y,2)) >= 35.22))
    {
        //Calcul d'angle en radian
        THETA[1] = acos((pow(x,2) + pow(y,2) - pow(LA,2) - pow(LB,2) )/(2 * LA * LB));
        THETA[0] = PI/2 - (atan2(y,x) - atan2(LB * sin(THETA[1]), LA + (LB * cos(THETA[1]))));
        

        //Transfert de radian à degré
        THETA[0] = ((-THETA[0] * 180 / PI)*epauleRatio)+(epauleZeroOffset*epauleRatio);
        THETA[1] = ((THETA[1] * 180 / PI))+coudeZeroOffset;

        // S'assurer que les angles ne cause pas de colision avec le bras
        if (THETA[0] < -90*1.667 || THETA[0] > 90*1.667 || THETA[1] < 0 || THETA[1] > 155 /*140*1.667*/ )
        {
            Serial.print("Erreur: Collision évitée : ");
            Serial.print(THETA[0]);
            Serial.print(" : ");
            Serial.println(THETA[1]);
            THETA[0] = 0+(epauleZeroOffset*epauleRatio);
            THETA[1] = 0+coudeZeroOffset;
        }
    }
    else
    {
        Serial.println("Erreur: Angles inatteignable");
        THETA[0] = 0+(epauleZeroOffset*epauleRatio);
        THETA[1] = 0+coudeZeroOffset;
    }
}

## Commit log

2023-01-25 Enlevé les fichiers
2023-01-25 Update gitignore pour tous les fichiers rebuild
2023-02-08 Ajout de actuators.cpp
2023-02-08 Ajout actuators.hpp
2023-02-08 Ajout reverseKinematics
    Erreur: Une position de x de 0 donne une division par 0...
    [Code_OpenCR.ino, inverseKinematics.cpp]
2023-02-08 process image fonctionne super bien wouhou
    [RGB_48.csv, RGB_crayons.csv, RGB_crayons2.csv]
2023-02-11 Debug inverseKinematics
    Changement des formules THETA[] et ajout de bonnes limites
2023-02-12 Ajout de fonction pour stepper motor et integration hall effect sensor
2023-02-15 Ajout fonctions envoi coordonnées
    [RGB_crayons.csv, RGB_crayons2.csv]
2023-02-15 Fix servo, fix cinematique joint 2, essaie stepper
    [Code_OpenCR.ino, actuators.cpp, inverseKinematics.cpp]
2023-02-19 Protocol de communication
2023-02-20 Mise à jour de la communication
2023-02-20 Revert "Fix servo, fix cinematique joint 2, essaie stepper"
    This reverts commit c7a47dbbba9c86fed8c73f97ddb0100db2292e03.
    [Code_OpenCR.ino, actuators.cpp, inverseKinematics.cpp]
2023-02-20 Enlèvement de la communication pour que le main compile
2023-02-22 Ajout des STL V1
    [Arm1_Cover.STL, Arm1_Cover2.STL, Arm1_Shell.STL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]
2023-02-22 Test d'angles
    Ajout d'une routine demo et tests unitaire des angles des deux joins
2023-02-22 Garder seulement les fichiers de communication
2023-02-22 Position_Tuning
    Ajout des offsets de tuning de position
2023-02-22 Librairie custom pour controle des steppers
    initial commit
2023-02-23 Update routines
    Ajout de Pick(), Place() et Square().
    changement de int a float pour la variable Displacementmm dans StepperZ
2023-02-24 variables et Pins
    ajout de nom de variables const au lieu des chiffres directement dans le code
    changement des pins step et dir du stepper
    ajout d'une routine de grid qui fait tous les point d'une grille 150x150 mm avec des points de 3 mm
2023-03-08 Reorg
    transfert des fonctions dans actuators.cpp
    ajout de stepperZ.cpp pour avoir acces dans actuators.cpp
2023-03-15 Update README.md
    Definition des sections
2023-03-15 Update LICENSE
    Changé de license de MIT à Apache 2.0
2023-03-16 Écriture sur papier
    ajout d'un fichier data.h qui contiens les points d'une forme a tracer, et changement temporaire dans le main pour le test de cette fonction
2023-03-19 Assemblage sur plaque finale
    Ajustement des positions du carrousel, Zoffset remplacé par un ajustement de l'angle de la surface de dessin, tests pour faire des lignes avec des fichiers externe
2023-03-20 Ajout main
    [RGB_20.csv, RGB_48.csv]
2023-03-21 Traduction française et ajustement pour une liste de données et non une matrice
2023-03-22 Ajout Centering Carrousel
    remplacement de la base du carrousel,
    ajout d'un servo pour ajuster la position et des movements dans la fonction index color,
    troubleshooting stepper driver,
2023-03-22 Clean main (stepper), Bon offset carousel
    2 crayons successifs
2023-03-22 modif main et bons crayons
    [RGB_20.csv]
2023-03-24 threads UI
    [RGB_48.csv]
2023-03-24 Bug choix de port regle
    [Code_OpenCR.ino, Communication.py, actuators.cpp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]
2023-03-24 switch case dans main
2023-03-27 Correction de la com des boutons
    [Code_OpenCR.ino, Communication.py, actuators.cpp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]
2023-03-27 Update check_port()
    Update connexion de la com automatique
2023-03-29 Retiré raspberry et ajouté la section des librairies à télécharger
2023-04-05 Clean Code_OpenCR, ajout de commentaire
2023-04-05 Create actuators.cpp
    Ajout en-tete
2023-04-05 Update stepperZ.cpp
    Ajout en-tête et traduction / ajout de commentaires EN FRANCAIS
2023-04-13 Changement des nom des contributeurs pour la communication
2023-09-20 optimisation Genie feminin
    - Changement du code de communication pour celui du ''hard-code'' avec les bouton de la OpenCR
    - ajustement de la hauteur maintenant possible d'aller plus précis qu'un mm entier
    - Ajustement vitesse de déplacement pour le bras à la sortie d'un crayon
    - Ajustement hauteur lorsque du tracage est fait
    - ajout des nouveaux design de pixel art
    - optimisation du code de tracage pour plus de rapidité
